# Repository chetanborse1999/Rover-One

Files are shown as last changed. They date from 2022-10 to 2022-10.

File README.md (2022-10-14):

# Rover-One
A Rover platform based on a Rocker Bogie suspension.

## About Project
The project demonstrates the Rocker Bogie suspension used in Mars Rovers. The assembly enables the chassis to remain stable over uneven surfaces and improves traction in soft terrain like sand. 

<p align="center">
  Home View
  Side View
  <br>
  <b>Fig. 1 and 2</b>
</p>

The robot has 6 wheels mounted on a servo that enables turning at variable turning radius, spot turns and strafing. The Rocker-Bogie assembly on each side is connected via a differential bar that maintains the chassis pitch on uneven surfaces. The chassis maintains an average pitch of both rockers.

<p align="center">
  <a href="https://youtu.be/0y1WFYk78O0" target="_blank">Showing Rocker Movement</a>
  <br><b>Showing movement of Rockers and Differential bar</b>
</p>

The robot has 6 Johnson motors and 6 MG995 servos powered by a Lithium Polymer battery. The actuators are controlled by Arduino Mega2560 and L298N H-bridge motor drivers. For communication, FS-i6/FS-ia6b radio transmitter/receiver is used. 

## CAD Model
Designed in Fusion360. Files are included. The chassis is made of 3x2 (35mmx23mm) aluminium tube. The remaining parts are 3d printed. 

<p align="center">
  CAD perspective
  <br>
  <b>Fig. 3 - Fusion360 Assembly</b>
</p>

## Hardware

1. Aluminium Tube Chassis.
2. 6 x MG995 metal gear servo with Disc metal horns
3. 6 x 12V Johnson Motors 200RPM with mounts
4. Arduino Mega2560
5. 3 x L298N motor drivers
6. DC-DC buck convertor
7. FS-i6/FS-ia6b Radio Transmitter/Receiver
8. Lipo Battery
9. Jumper Wires
10. Fasteners

## Instruction to Run

1. Make connections using jumper for motor drivers, servos and radio RX module (not required for serial). Pins are defined in the accompanying header file. Ensure that Enable pins are not using pins 44, 45 and 46 on Mega since they do not have pwm when Servo.h is used. 
2. Map the value to be written to servos such that wheel is in forward position when writing '90' as shown in fig. 1.
3. Upload code to Mega. 
4. Power the motors with 12v and Servos with 5v from a voltage regulator, preferably buck convertor. Ensure that microcontroller has a seperate power source as fluctuations can cause it to reboot.
5. On the Transmitter, configure channel 5 and 6 to swA and swC.
6. Two Methods to run:
    
    1. To run using Radio transmitter: Power the Mega, Turn on the radio Transmitter. Set swC to position 2. Now connect the battery. All servos should move to default position and can be steered using right stick. Now move swA to position 2 to arm the motors. 
    
        The bot is now mobile. Use right stick to give move forward/backward as well as steer. To switch to strafe mode, move swC to position 1 and use left stick to strafe. To switch to spot rotation mode, move swC to position 3 and use left stick to spot rotate right/left. swA can be used in any mode to arm or disarm the motors.

    2. To run using Serial, upload serial_ctrl code. Ensure jumpers are connected to pins specified in the code. A Standard USB or USB to TTL convertor can be used (Only RX pin on arduino required, unless debugging). Now launch the accompanying python script 'get_keys.py'. The keyboard library is required to run this script. Now standard WASD controls can be used to control the bot. Strafe mode not available yet.

## Videos

<p align="center">
  <a href="https://youtu.be/RismbZGRqcw" target="_blank">Showing different drive modes</a>
  <br><b>Different drive modes</b><br><br>
  <a href="https://youtu.be/btVR41I81UQ" target="_blank">Showing going over some obstacle</a>
  <br><b>Going over an obstacle</b><br>
</p>

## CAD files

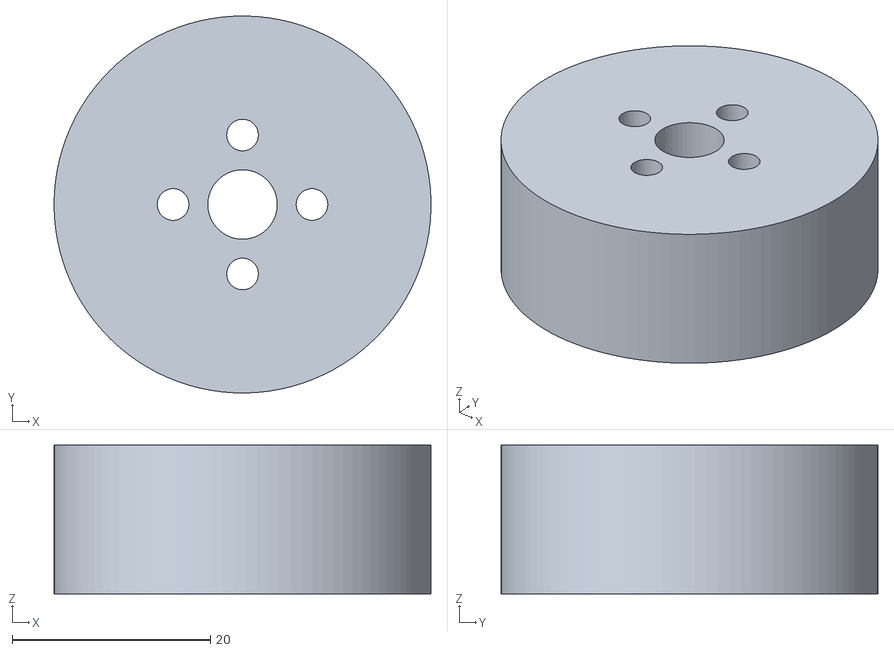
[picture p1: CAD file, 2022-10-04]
stls/disc.stl
38.0 x 38.0 x 15.0

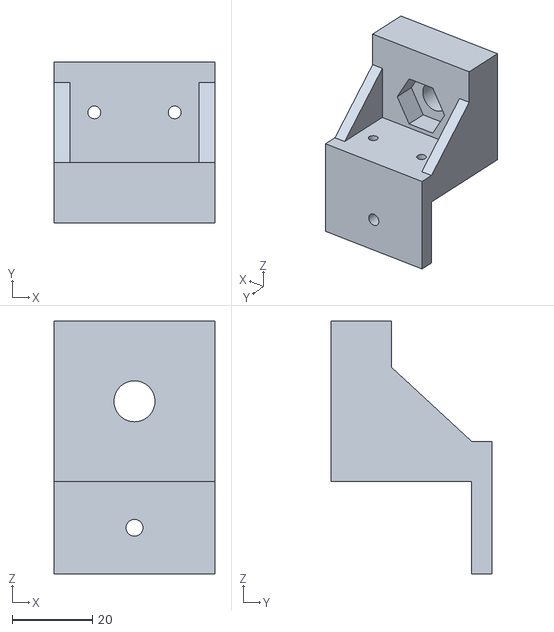
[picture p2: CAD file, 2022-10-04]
stls/rocker_mount.stl
40.0 x 40.0 x 63.0

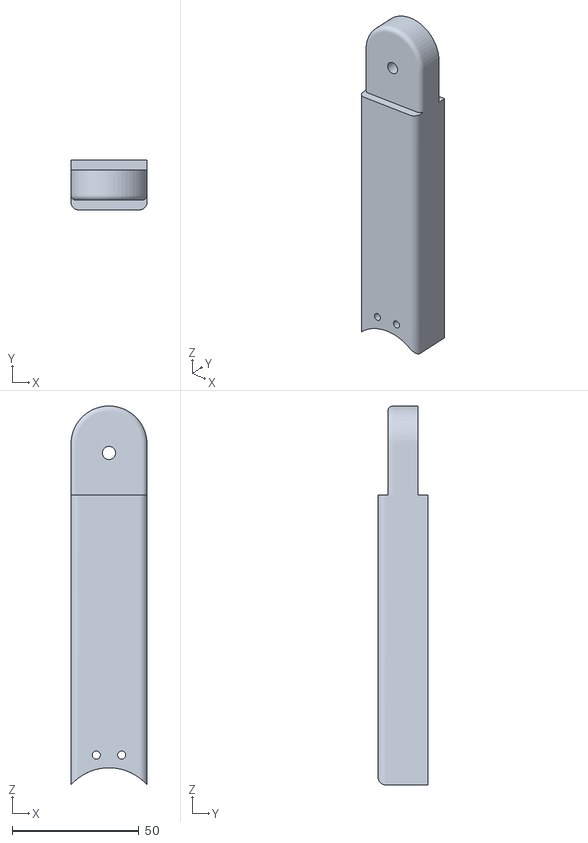
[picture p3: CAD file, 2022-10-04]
stls/rocker_pivot_new.stl
30.0 x 19.6 x 149.3

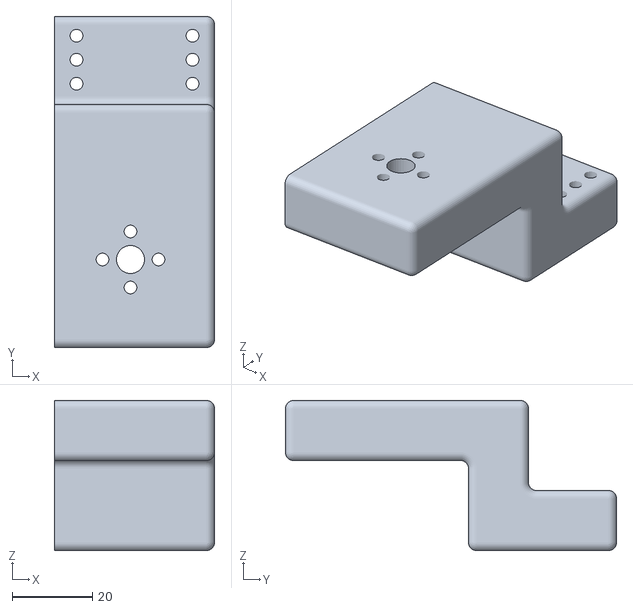
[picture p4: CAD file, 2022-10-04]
stls/tetris.stl
40.0 x 82.8 x 37.5

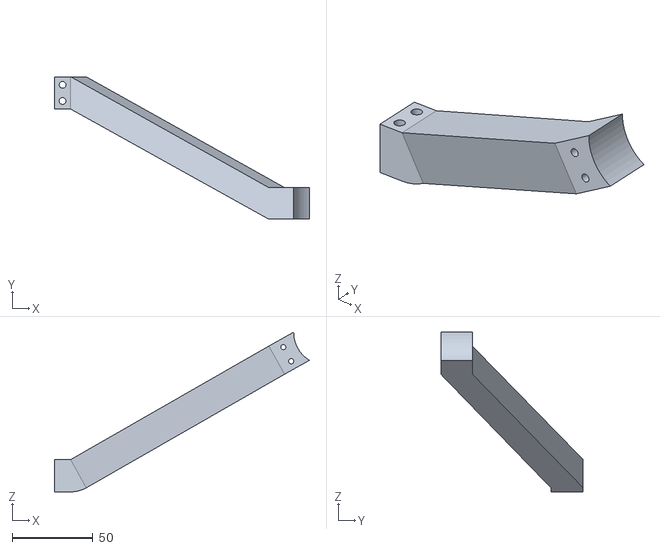
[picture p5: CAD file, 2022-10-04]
stls/rocker_long_arm_mirrored.stl
158.0 x 88.3 x 99.0

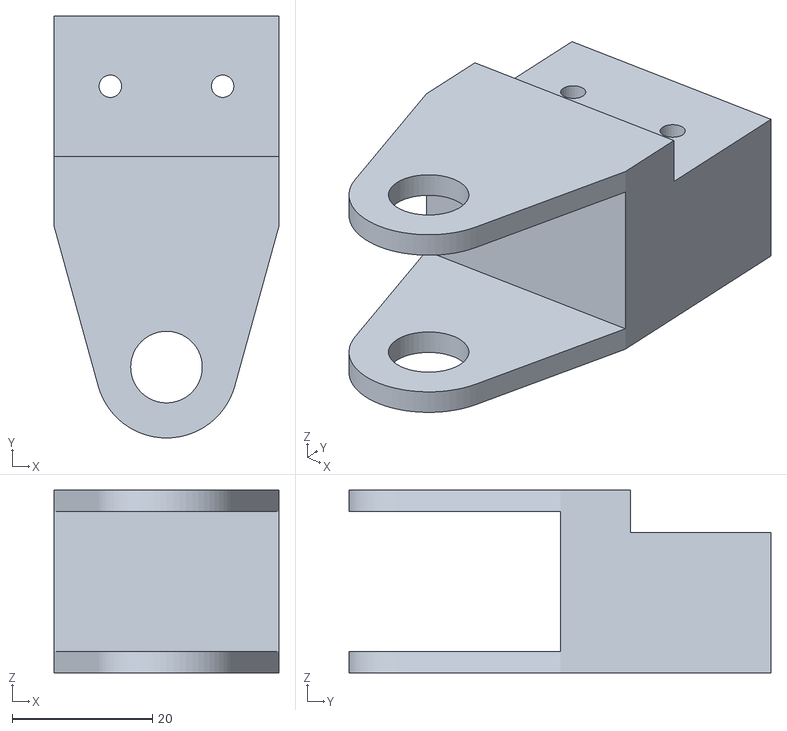
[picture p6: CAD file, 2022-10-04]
stls/diff_pivot.stl
32.0 x 60.1 x 26.0

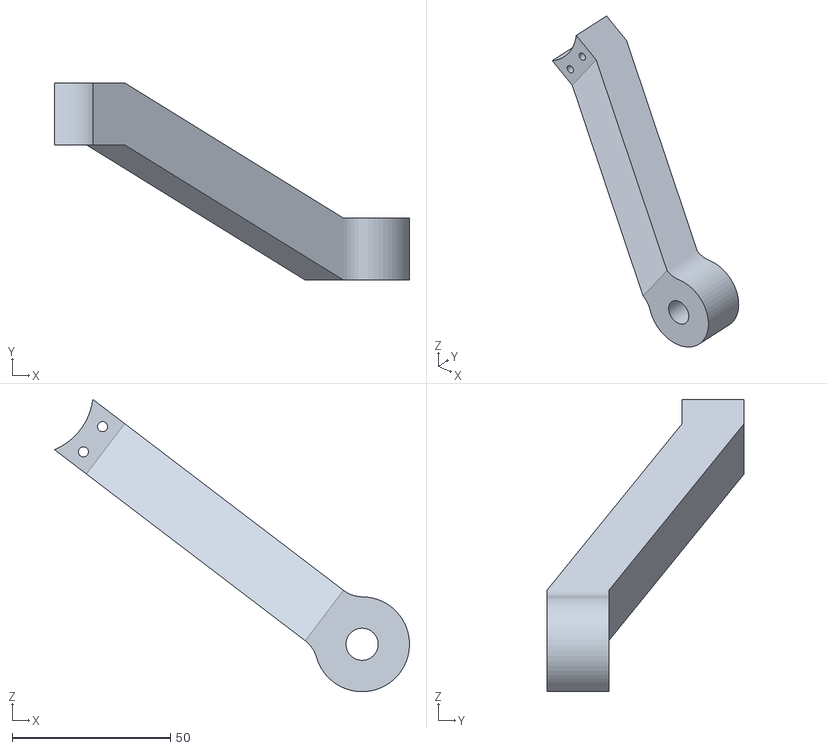
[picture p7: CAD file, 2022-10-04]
stls/rocker_short_arm.stl
112.3 x 62.4 x 92.4

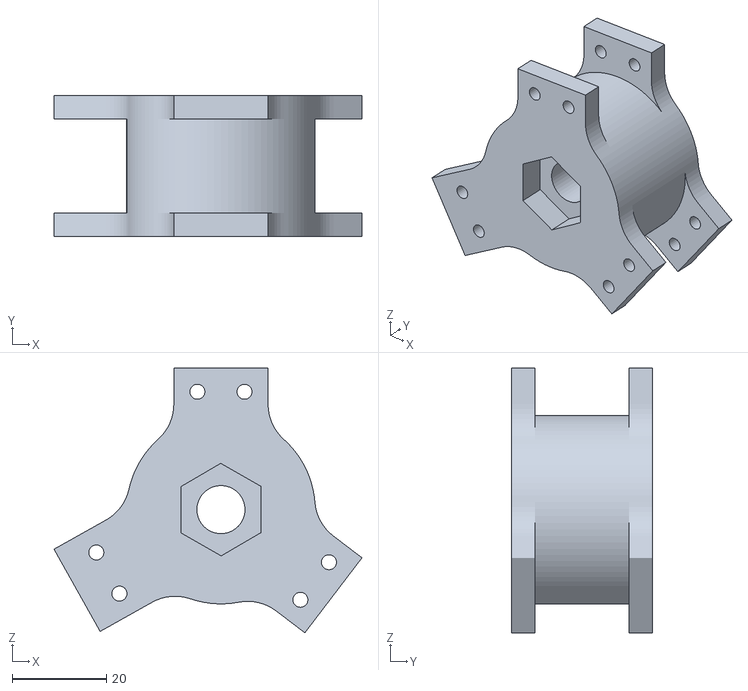
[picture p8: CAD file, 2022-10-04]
stls/rocker_hub.stl
65.3 x 30.0 x 56.1

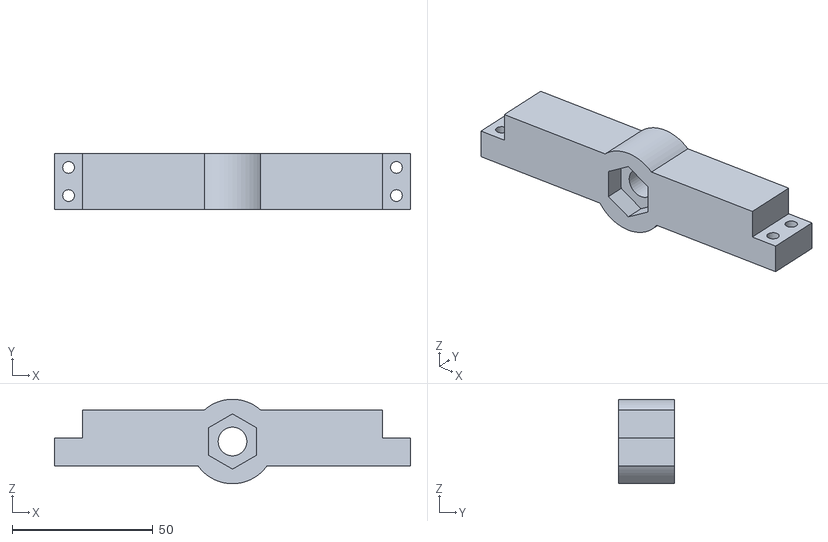
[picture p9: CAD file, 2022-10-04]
stls/bogie_bar.stl
126.5 x 20.0 x 30.0

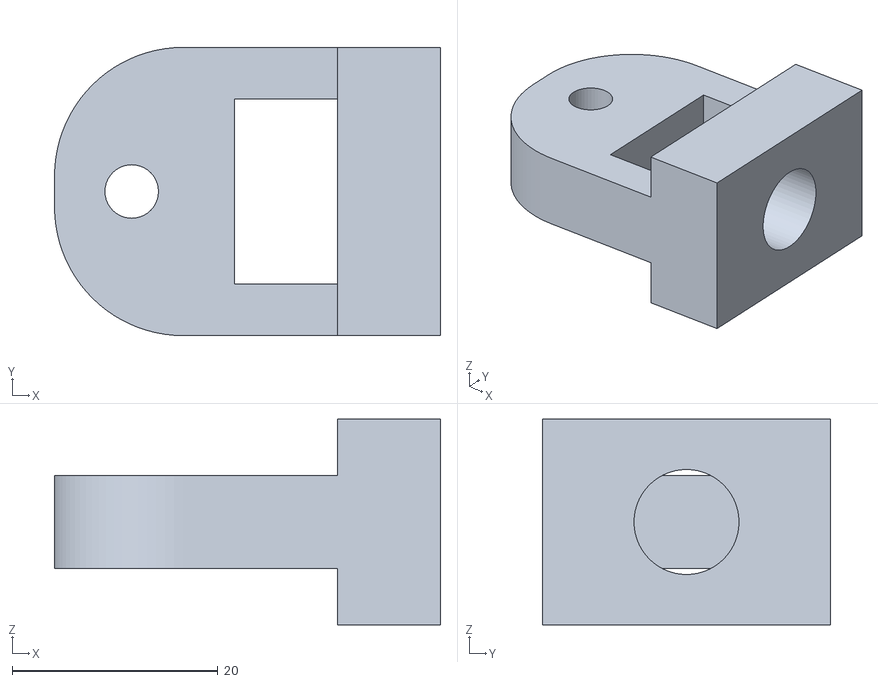
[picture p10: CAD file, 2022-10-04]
stls/link_2.stl
37.5 x 28.0 x 20.0

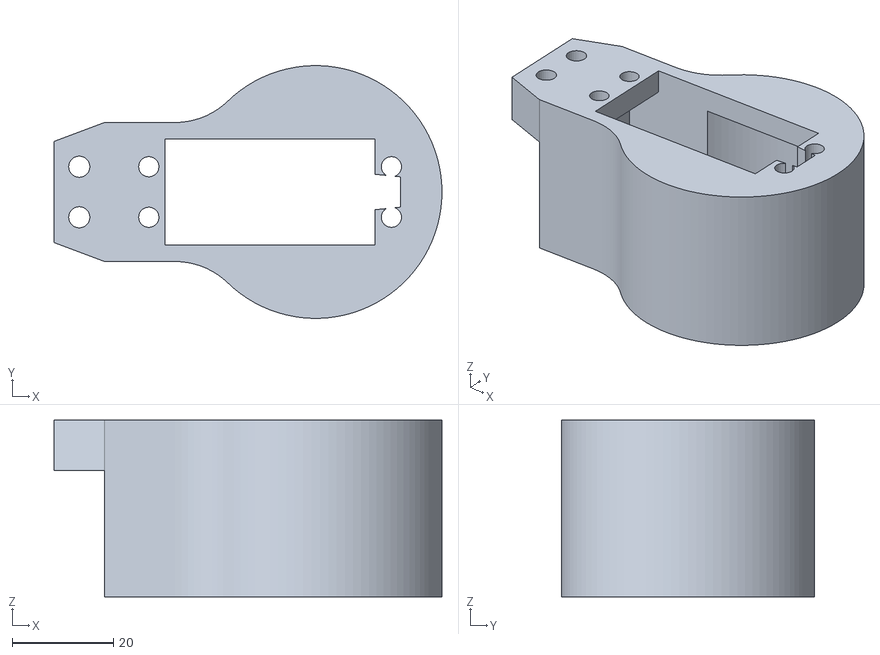
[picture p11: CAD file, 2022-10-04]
stls/servo_hub.stl
76.8 x 50.0 x 35.0

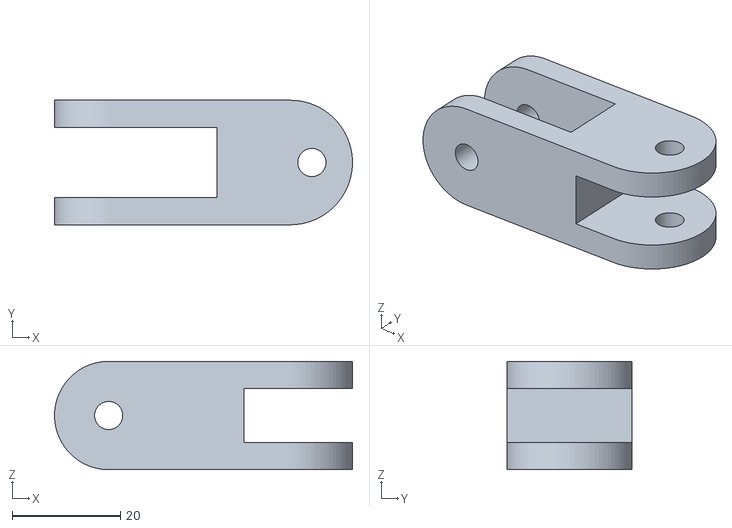
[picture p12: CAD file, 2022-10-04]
stls/link_1.stl
55.0 x 23.0 x 20.0

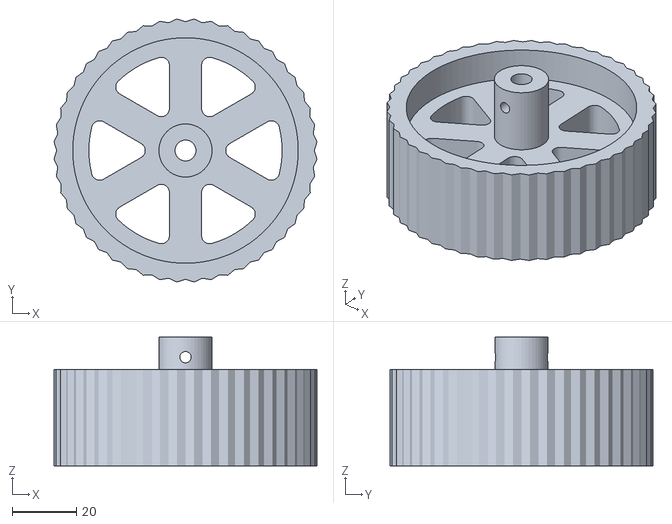
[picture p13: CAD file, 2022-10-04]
stls/wheel.stl
81.7 x 81.7 x 40.0

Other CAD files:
stls/rocker_long_arm.stl
fusion360 files/bogie_assembly.f3z
fusion360 files/diff_pivot.f3d
fusion360 files/disc.f3d
fusion360 files/link_1.f3d
fusion360 files/link_2.f3d
fusion360 files/rocker.f3d
fusion360 files/rocker_mount.f3d
fusion360 files/servo_hub.f3z
fusion360 files/tetris.f3d
fusion360 files/wheel.f3d

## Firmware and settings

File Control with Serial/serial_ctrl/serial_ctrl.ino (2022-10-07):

#include <Servo.h>
#include <math.h>
Servo servo_obj[6];
const int servo_pins[6] = {22,24,26,28,30,32};
const int motor_pins[6][3] = {{3,37,35},{2,23,25},{4,31,33},{6,27,29},{5,50,48},{7,42,40}};

String x = "";

const int WIDTH=300;
const int LENGTH=210;
const int BASE_SPEED=100;
const int servo_range[6][2] = {{10,160},{15,165},{12,168},{10,210},{10,194},{5,189}};// (0deg value, 180deg value)
float servo_values[7] = {0,0,0,0,0,0,0};
float motor_values[6] = {0,0,0,0,0,0};

void setup() {
  Serial.begin(115200);
  pinMode(13, OUTPUT);
  for (int i=0;i<6;i++){
    servo_obj[i].attach(servo_pins[i]);
  }
}

//    float y = 210*tan((target)*3.14/180);
//    float x = 210+300*tan((target)*3.14/180);
//    target_a = atan2(y,x)*180/3.14;

void write_motors(int pins[3], float value){
  if (value>0){
    digitalWrite(pins[1], HIGH);
    digitalWrite(pins[2], LOW);
  }
  else if (value<0){
    digitalWrite(pins[1], LOW);
    digitalWrite(pins[2], HIGH);
  }
  else{
    digitalWrite(pins[1], LOW);
    digitalWrite(pins[2], LOW);
  }
  Serial.println(pins[0]);
  Serial.println(value);
  analogWrite(pins[0], abs(value));
}

void extract_data(String cmd){
    if (cmd.substring(0,1)=="R"){
      String dir = cmd.substring(1,3);
      int target = cmd.substring(3).toInt();
      
      if (target>30 || target<-30){
        digitalWrite(13, HIGH);
      }
      else{
        digitalWrite(13, LOW);
      }
      
      Serial.println(target);
      if (target>=0){
        servo_values[6]=1;
      }
      else{
        servo_values[6]=0;
      }
      
      float y = LENGTH*tan(abs(target)*PI/180);
      float x = LENGTH+WIDTH*tan(abs(target)*PI/180);
      float target2 = atan2(y,x)*180/PI;
//      Serial.println(target2);
      float speed0, speed1, speed4;
      if (target!=0){
        speed0 = BASE_SPEED * sin(abs(target)*PI/180) / sin(target2*PI/180);
        speed1 = BASE_SPEED * sin(abs(target)*PI/180) / tan(target2*PI/180);
        speed4 = BASE_SPEED * sin(abs(target)*PI/180) / tan(abs(target)*PI/180);
      }
      else if (target==0){
        speed0 = BASE_SPEED;
        speed1 = BASE_SPEED;
        speed4 = BASE_SPEED;
      }
      motor_values[3]=motor_values[5]=BASE_SPEED;
      motor_values[2]=motor_values[0]=speed0;
      motor_values[1]=speed1;
      motor_values[4]=speed4;

      servo_values[3]=abs(target)+90;
      servo_values[4]=90;
      servo_values[5]=-abs(target)+90;
      servo_values[0]=target2+90;
      servo_values[1]=90;
      servo_values[2]=-target2+90;
      
      if (dir=="FD"){
        Serial.println("Forward");
      }
      else if (dir=="BK"){
        Serial.println("Backward");
        for (int i=0;i<6;i++){
          motor_values[i]=-motor_values[i];
        }
      }
      
      else if (dir.substring(0,1)=="S"){
        float spot_angle = atan2(LENGTH,WIDTH/2)*180/PI;
        servo_values[0]=servo_values[5]=90+spot_angle;
        servo_values[2]=servo_values[3]=90-spot_angle;
        servo_values[1]=servo_values[4]=90;
        for(int i=0;i<6;i++){motor_values[i]=0;}
        if (dir.substring(1,2)=="R" || dir.substring(1,2)=="L"){
          motor_values[0]=motor_values[2]=motor_values[3]=motor_values[5]=BASE_SPEED;
          motor_values[1]=motor_values[4]=BASE_SPEED * (WIDTH/2) / sqrt(pow(WIDTH/2,2)+pow(LENGTH,2));
        }
        else{Serial.println("SpotMode");}
        servo_values[6]=1;
        if (dir=="SR"){
          Serial.println("SpotRight");
          for (int i=3;i<6;i++){
            motor_values[i]=-motor_values[i];
          }
        }
        else if (dir=="SL"){
          Serial.println("SpotLeft");
          for (int i=0;i<3;i++){
            motor_values[i]=-motor_values[i];
          }
        }
      }
    
      else{
        Serial.println("Default(STOP)");
        for (int i=0;i<6;i++){
          motor_values[i]=0;
        }
      }
    }
}

void drive(float servos[7], float motors[6]){
  if (servos[6]==1){
    for (int i=0;i<6;i++){
      servos[i] = map(servos[i], 0, 180, servo_range[i][0], servo_range[i][1]);
      servo_obj[i].write(servos[i]);
      write_motors(motor_pins[i], motors[i]);
//      Serial.print("Servo ");Serial.print(i);Serial.print(" ");Serial.println(servos[i]);
//      Serial.print("Motor ");Serial.print(i);Serial.print(" ");Serial.println(motors[i]);Serial.println(" ");
    }
  }
  else{
    for (int i=0;i<6;i++){
      servos[5-i] = map(servos[5-i], 0, 180, servo_range[i][0], servo_range[i][1]);
      servo_obj[i].write(servos[5-i]);
      write_motors(motor_pins[i], motors[5-i]);
//      Serial.print("Servo ");Serial.print(i);Serial.print(" ");Serial.println(servos[5-i]);
//      Serial.print("Motor ");Serial.print(i);Serial.print(" ");Serial.println(motors[5-i]);Serial.println(" ");
    }
  }
}


int readflag = 0;
void loop() {
  while (Serial.available()>0){
    char inByte = Serial.read();
    if (inByte==60){
      readflag = 1;
    }
    else if (inByte==38){
//        Serial.println(x);
        extract_data(x);
        x = "";
    }
    else if (inByte==62){
//        Serial.println("ok");
        drive(servo_values, motor_values);
        readflag = 0;
    }
    else{
      if (readflag){
        x = x + inByte;
      }
    }
  }
}

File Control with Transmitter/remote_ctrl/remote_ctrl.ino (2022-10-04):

#include "rpins.h"
#include <Servo.h>
#include <math.h>

Servo servo_obj[6];

const int WIDTH = 300;
const int LENGTH = 210;
const int servo_range[6][2] = {{10,160},{15,165},{12,168},{10,210},{10,194},{5,189}};
float servo_values[7] = {0,0,0,0,0,0,0};
float motor_values[6] = {0,0,0,0,0,0};

int read_sticks(int channel){
  int chvalue = pulseIn(channel, HIGH);
  if (chvalue>1900){
    chvalue=1900; 
  }
  else if (chvalue<1100){
    chvalue=1100;
  }
  return chvalue;
}

int read_switches(int channel){
  int chvalue = pulseIn(channel, HIGH);
  if (channel==CH5){
    chvalue = (chvalue>1500) ? 2 : 1;
  }
  else if (channel==CH6){
    if (chvalue<1250){
      chvalue = 1;
    }
    else if (chvalue>1900){
      chvalue = 3;
    }
    else{
      chvalue = 2;
    }
  }
  return chvalue;
}

void setup() {
  Serial.begin(115200);
  
  pinMode(13, OUTPUT);
  digitalWrite(13, HIGH);
  
  pinMode(CH1, INPUT);
  pinMode(CH2, INPUT);
  pinMode(CH3, INPUT);
  pinMode(CH4, INPUT);
  pinMode(CH5, INPUT);
  pinMode(CH6, INPUT);  

  for (int i=0;i<6;i++){
    servo_obj[i].attach(servo_pins[i]);
  }
}

int ch1value, ch2value, ch3value, ch4value, ch5value, ch6value;

void calculate(int angle, int throttle, int spot_throttle, int swA, int swC){
  if (angle>30 || angle<-30){
    digitalWrite(13, HIGH);
  }
  else{
    digitalWrite(13, LOW);
  }

  servo_values[6] = (angle>0) ? 1 : 0;

  //calc angles
  float y = LENGTH*tan(abs(angle)*PI/180);
  float x = LENGTH+WIDTH*tan(abs(angle)*PI/180);
  float angle2 = atan2(y,x)*180/PI;
  //store angles
  servo_values[0]=angle2+90;
  servo_values[1]=90;
  servo_values[2]=-angle2+90;
  servo_values[3]=abs(angle)+90;
  servo_values[4]=90;
  servo_values[5]=-abs(angle)+90;

  //speed calc
  float speed0, speed1, speed4;
  if (angle==0){
    speed0 = speed1 = speed4 = throttle;
  }
  else{
    speed0 = throttle * sin(abs(angle)*PI/180) / sin(angle2*PI/180);
    speed1 = throttle * sin(abs(angle)*PI/180) / tan(angle2*PI/180);
    speed4 = throttle * sin(abs(angle)*PI/180) / tan(abs(angle)*PI/180);
  }
  //store speed
  motor_values[0] = motor_values[2] = speed0;
  motor_values[3] = motor_values[5] = throttle;
  motor_values[1] = speed1;
  motor_values[4] = speed4;

  if (swA!=2){
    for (int i=0;i<6;i++){
      motor_values[i]=0;
    }
  }
  
  if (swC==1){
    servo_values[0]=servo_values[1]=servo_values[2]=servo_values[3]=servo_values[4]=servo_values[5]=0;
    if (swA==2){
      motor_values[0]=motor_values[1]=motor_values[2]=motor_values[3]=motor_values[4]=motor_values[5]=-spot_throttle*2;
    }
  }

  else if (swC==3){
    servo_values[6]=1;
    float spot_angle = atan2(LENGTH, WIDTH/2)*180/PI;
    servo_values[0]=servo_values[5] = 90+spot_angle;
    servo_values[2]=servo_values[3] = 90-spot_angle;
    servo_values[1]=servo_values[4] = 90;
    if (swA==2){
      //calc spot motor val using spot_throttle
      motor_values[0]=motor_values[2] = spot_throttle;
      motor_values[3]=motor_values[5] = -spot_throttle;
      motor_values[1]=spot_throttle * (WIDTH/2) / sqrt(pow(WIDTH/2,2)+pow(LENGTH,2));
      motor_values[4]=-spot_throttle * (WIDTH/2) / sqrt(pow(WIDTH/2,2)+pow(LENGTH,2));
    }
  }
}

void drive(float servos[7], float motors[6]){
  if (servos[6]==1){
    for (int i=0;i<6;i++){
      servos[i]=map(servos[i], 0, 180, servo_range[i][0], servo_range[i][1]);
      servo_obj[i].write(servos[i]);
      write_motors(motor_pins[i], motors[i]);
//      Serial.print("Servo ");Serial.print(i);Serial.print(" ");Serial.println(servos[i]);
//      Serial.print("Motor ");Serial.print(i);Serial.print(" ");Serial.println(motors[i]);Serial.println(" ");
    }
  }
  else{
    for (int i=0;i<6;i++){
      servos[5-i]=map(servos[5-i], 0, 180, servo_range[i][0], servo_range[i][1]);
      servo_obj[i].write(servos[5-i]);
      write_motors(motor_pins[i], motors[5-i]);
//      Serial.print("Servo ");Serial.print(i);Serial.print(" ");Serial.println(servos[5-i]);
//      Serial.print("Motor ");Serial.print(i);Serial.print(" ");Serial.println(motors[5-i]);Serial.println(" ");
    }
  }
}

void write_motors(int pins[3], float value){
  if (value>0){
    digitalWrite(pins[1], HIGH);
    digitalWrite(pins[2], LOW);
  }
  else if (value<0){
    digitalWrite(pins[1], LOW);
    digitalWrite(pins[2], HIGH);
  }
  else{
    digitalWrite(pins[1], LOW);
    digitalWrite(pins[2], LOW);
  }
  Serial.println(pins[0]);
  Serial.println(value);
  analogWrite(pins[0], abs(value));
}

void loop() {
  ch1value = read_sticks(CH1);
  ch2value = read_sticks(CH2);
  ch3value = read_sticks(CH3);
  ch4value = read_sticks(CH4);
  ch5value = read_switches(CH5);
  ch6value = read_switches(CH6);
  
  ch1value = map(ch1value, 1100, 1900, -45, 45);
  ch2value = map(ch2value, 1100, 1900, -100, 100);
  ch3value = map(ch3value, 1100, 1900, -100, 100);
  ch4value = map(ch4value, 1100, 1900, -100, 100);

  if (ch1value<10 && ch1value>-10) ch1value=0;
  if (ch2value<20 && ch2value>-20) ch2value=0;
  if (ch3value<20 && ch3value>-20) ch3value=0;
  if (ch4value<20 && ch4value>-20) ch4value=0;
//  Serial.println("");
  Serial.println(ch1value);
  Serial.println(ch2value);
//  Serial.println(ch2value);
//  Serial.println(ch3value);
//  Serial.println(ch4value);
//  Serial.println(ch5value);
//  Serial.println(ch6value);
  calculate(ch1value, ch2value, ch4value, ch5value, ch6value);
  drive(servo_values, motor_values);
}
